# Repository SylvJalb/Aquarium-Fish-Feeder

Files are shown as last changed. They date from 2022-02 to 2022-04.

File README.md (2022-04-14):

# Aquarium Fish Feeder

## Step 1 : Print alls parts

For this, you need a 3D printer and ~100g of plastic (PLA).     

Find all stl files in the folder "3D_print" and print them.     
Instructions:   
- Nozzle: 0.4 mm
- Filament: PLA
- Layer height: 0.2 mm
- Infill: 10%
- Support: Yes for `Holder` (60°), No for Other parts
- Wall thickness: 2.0 mm (5 wall lines count) for `Holder`, By default for Other parts
- Disable "Union overlapping Volumes"

## Step 2 : Assemble all parts
For that, you can see my video [on YouTube](https://www.youtube.com/watch?v=yZgBFvdJES4). ([5:02](https://youtu.be/yZgBFvdJES4?t=302))    
Sylvain Jalbert - YouTube (https://www.youtube.com/watch?v=yZgBFvdJES4)

## Step 3 : Install raspbian on your Raspberry Pi
1. Download [Raspbian OS](https://howtoraspberrypi.com/downloads/)    
1. Flash a SD card with the zip file by using [balenaEtcher](https://www.balena.io/etcher/) (for exemple)    
1. Plug the SD card into the Raspberry Pi and turn on the power.       
1. Follow the instructions on the screen to install the Raspbian OS.    

## Step 4 : Import the repo on your Raspberry Pi
```bash
git clone https://github.com/SylvJalb/Aquarium-Fish-Feeder.git
cd Aquarium-Fish-Feeder
```

## Step 5 : Installations
```bash
pip3 install -r requirements.txt
```
Make sure you have gunicorn installed. Do the command `which gunicorn` and make sure you have the good path in `run.sh` (last line).   

Then define your environment variables in env.py (`nano env.py`):
```python
timezone_name = "Europe/Paris" # Your timezone
pwm_gpio = 12 #Use pin 12 for PWM signal
frequence = 50

# Positions of the servo (in degrees)
posFeed = 160   #Position to drop the food
posReload = 30  #Position to reload the food
```

## Step 6 : Network configurations
Go on your internet router panel and configure your DHCP to define static IP to your Raspberry Pi.     
Open the port number in your router panel and configure it to your Raspberry Pi. (tcp protocol)

## Step 7 : Start the service
```bash
./run.sh
```
----------
If you want to automatically start the service at boot, create `/etc/systemd/system/feeder.service` file:
```bash
sudo nano /etc/systemd/system/feeder.service
```
Paste this content, then **modify paths** to your files:  
```bash
[Unit]
Description=feeder service

[Service]
User=pi
WorkingDirectory=/home/pi/Aquarium-Fish-Feeder
ExecStart=/bin/bash /home/pi/Aquarium-Fish-Feeder/run.sh
Restart=always

[Install]
WantedBy=multi-user.target
```     
Then, do `sudo systemctl enable feeder.service` to activate the auto-start of the service after each startup.

To start the service, do `sudo systemctl start feeder.service`

----------

## Step 8 : IFTTT configuration
Go on your IFTTT account and create a new webhook.
Add a Applet : **IF** you condition... **THEN** use webhook like this:

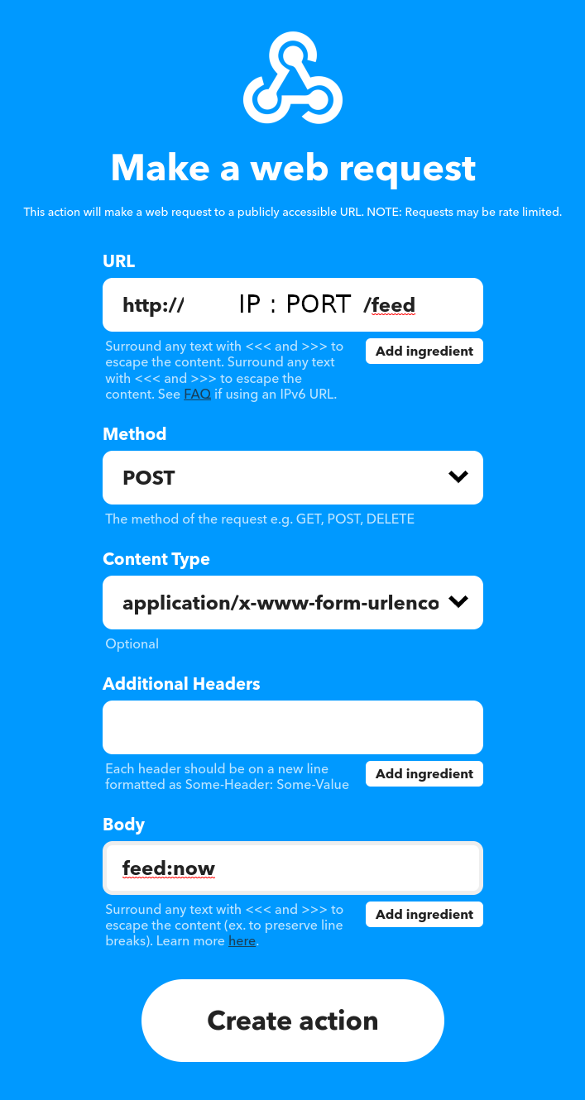
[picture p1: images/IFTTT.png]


# Log visualization
Now you can see the logs (dates when the feeder have been feeded) on this link:     
http://YOUR_IP_ADDRESS:PORT/feed

# Sources
https://raspberry-pi.fr/servomoteur-raspberry-pi/       
https://pythonbasics.org/flask-http-methods/

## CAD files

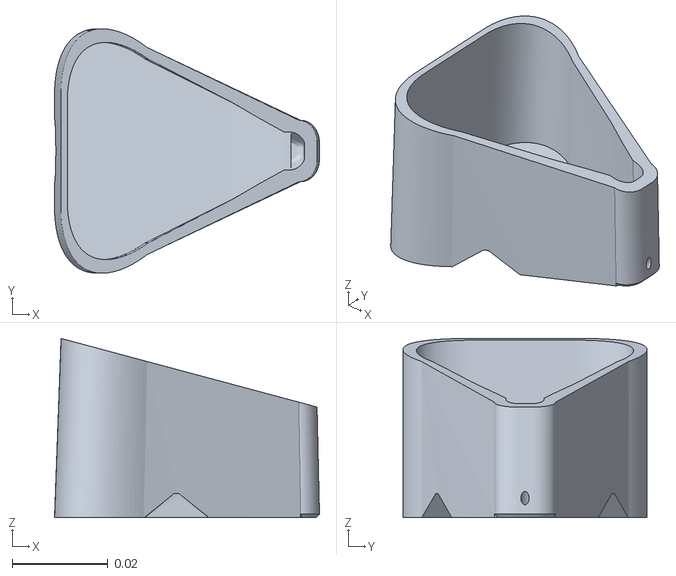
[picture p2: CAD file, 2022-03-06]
3D_print/Container.stl
0.0552 x 0.0509 x 0.0373

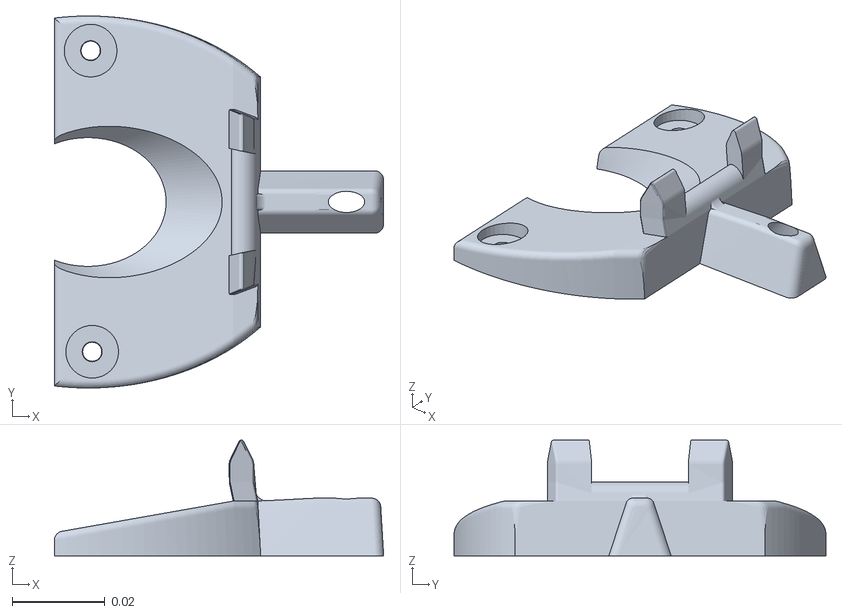
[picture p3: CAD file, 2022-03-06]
3D_print/Plate.stl
0.0708 x 0.08 x 0.0249

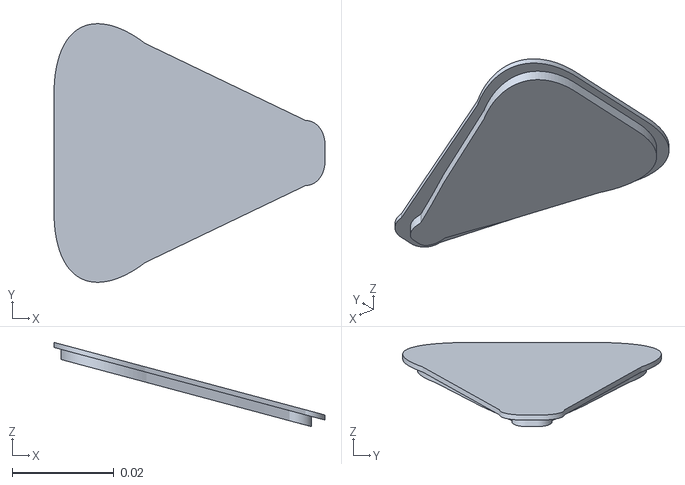
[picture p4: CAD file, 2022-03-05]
3D_print/Container_lid.stl
0.0534 x 0.0509 x 0.0166

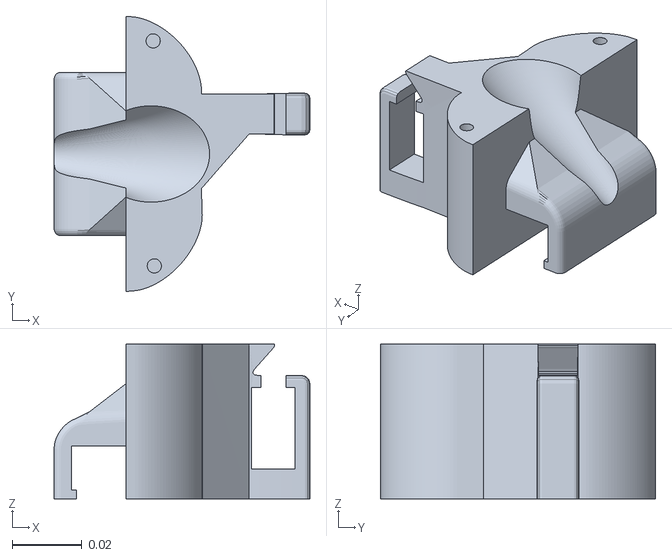
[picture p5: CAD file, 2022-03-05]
3D_print/Holder.stl
0.0736 x 0.0791 x 0.0446

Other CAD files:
feeder.blend

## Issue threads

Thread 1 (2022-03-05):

Food blocks the system

SylvJalb, 2022-03-05:
The pellets wedge themselves between the container and the plate.
This causes the system to crash without the error being reported to the server.
You must then unlock the mechanism by hand !

I think we need to fully redesign the system...

SylvJalb, 2022-03-14:
The system has been redesigned

Closed 2022-03-14.

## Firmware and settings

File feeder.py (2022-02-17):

import datetime
import os
from flask import Flask
from flask import request
from pytz import timezone

from env import *
from servo import *

app = Flask(__name__)


@app.route('/')
def hello():
    return 'Hello, World!'

@app.route('/feed', methods=['GET', 'POST'])
def feed():
    log_file = "./feeder.log"
    if request.method == 'GET':
        # Check if the log file exists
        if os.path.isfile(log_file):
            # return content of feeder.log
            with open(log_file, 'r') as f:
                content = f.read()
            # replace newline with <br>
            content = content.replace('\n', '<br>')
            return content
        else:
            return "No log file found."
    if request.method == 'POST':
        when = request.form['feed']
        if when == 'now':
            # feed now
            feedOneTime()
            with open(log_file, 'a') as f:
                # write time without microseconds
                f.write("\n" + str(datetime.datetime.now(timezone(timezone_name)).replace(microsecond=0)))
            return 'OK ! I drop some food...'
    with open(log_file, 'a') as f:
            f.write("\n"  + str(datetime.datetime.now(timezone(timezone_name)).replace(microsecond=0)) + " Problem with the request")
    return 'Problem with your request...'

if __name__ == '__main__':
   app.run(debug = True)

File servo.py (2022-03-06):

#!/usr/bin/env python3
#-- coding: utf-8 --
import RPi.GPIO as GPIO
import time
from env import *

#Set function to calculate percent from angle
def angle_to_percent (angle) :
    if angle > 180 or angle < 0 :
        return False

    start = 4
    end = 12.5
    ratio = (end - start)/180 #Calcul ratio from angle to percent

    angle_as_percent = angle * ratio

    return start + angle_as_percent



def feedOneTime():
    GPIO.setmode(GPIO.BOARD) #Use Board numerotation mode
    GPIO.setwarnings(False) #Disable warnings

    GPIO.setup(pwm_gpio, GPIO.OUT)
    pwm = GPIO.PWM(pwm_gpio, frequence)

    # Go at posReload° position to reload the servo
    # Go slowly to avoid damage
    pwm.start(angle_to_percent(posReload))
    time.sleep(2)

    # Finish at posFeed° position to drop the food
    pwm.ChangeDutyCycle(angle_to_percent(posFeed))
    time.sleep(1)

    #Close GPIO & cleanup
    pwm.stop()
    GPIO.cleanup()

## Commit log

2022-02-12 first 3D draw
    [feeder.blend]
2022-02-15 change form
    [feeder.blend]
2022-02-16 Finish to design all parts
    [Container.stl, Container_Holder.stl, Holder.stl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]
2022-02-16 plate_001 correction surface bug
    [Plate_001.stl, feeder.blend]
2022-02-17 increase control servo hole in 3D files
    [Plate_001.stl, feeder.blend]
2022-02-17 try to move the servo controller
2022-03-03 remake 3D files
    [Case.stl, Container.stl, Container_Holder.stl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]
2022-03-03 new prints instructions
    [Case.stl, Container.stl, Container_Lid.stl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]
2022-03-04 improve 3D files
    [Container.stl, Mechanism.stl, feeder.blend]
2022-03-05 Try a new approach | NEW DESIGN
    [Case.stl, Container.stl, Container_Lid.stl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]
2022-03-06 refine container to prevent blocking
    [Container.stl, Plate.stl, feeder.blend]
2022-03-06 define positions of the servo in env file
